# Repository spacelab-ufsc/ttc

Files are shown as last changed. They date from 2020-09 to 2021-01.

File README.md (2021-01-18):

<h1 align="center">
    TELEMETRY, TRACKING AND COMMAND
    <br>
</h1>

<h4 align="center">Telemetry, Tracking and Command module designed and developed by SpaceLab.</h4>

<p align="center">
	<a href="https://github.com/spacelab-ufsc/spacelab#versioning">
		
	</a>
	<a href="https://github.com/spacelab-ufsc/ttc/releases">
		
	</a>
	<a href="https://github.com/spacelab-ufsc/ttc/releases">
		
	</a>
	<a href="https://github.com/spacelab-ufsc/ttc/commits/master">
		
	</a>
	<a href="https://github.com/spacelab-ufsc/ttc/issues">
		
	</a>
	<a href="https://github.com/spacelab-ufsc/ttc/graphs/contributors">
		
	</a>
	<a href="#license">
		
	</a>
	<a href="https://github.com/floripasat/ttc">
		
	</a>
</p>

<p align="center">
    <a href="#overview">Overview</a> •
    <a href="#license">License</a> •
    <a href="#releases">Releases</a> •
</p>

<p align="center">
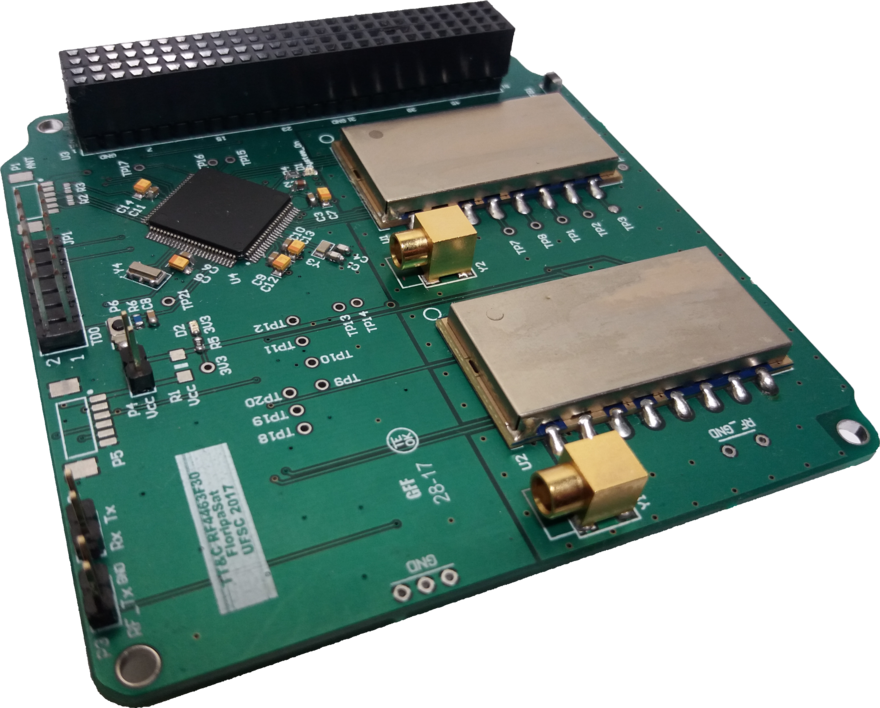
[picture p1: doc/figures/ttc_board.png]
    
</p>

## Overview

The TTC (or TT&C) is the communication module of the CubeSats from SpaceLab. It is responsible to make the communication between the earth (a ground station) and a satellite, and is divided in two sub-modules: Beacon and telemetry.

The beacon is a independent sub-module who transmits a periodic signal containing an identification data (ID) of the satellite and some basic telemetry data. The telemetry sub-module is the main communication device. It has a bidirectional data link to receive telecommands from the earth and transmit all the requested data. The telemetry sub-module is controlled by an external device (as example, an OBDH module).

## License

This project is open-source under three different licenses: GNU General Public License v3.0 for firmware sources, CERN Open Hardware License v2.0 for hardware files, and CC BY-SA 4.0 for the documentation. Some third-part files and libraries are subjected to their specific terms and licenses.

## Releases

The TTC software and hardware releases are synchronized in order to garantee compatibility. Then, using diferent versions might lead to unpredictable behavior. Refer to the [documentation](https://github.com/spacelab-ufsc/ttc/tree/master/doc) for compatibility notes.

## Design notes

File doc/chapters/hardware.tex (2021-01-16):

%
% hardware.tex
%
% Copyright (C) 2021 by SpaceLab.
%
% TTC Documentation
%
% This work is licensed under the Creative Commons Attribution-ShareAlike 4.0
% International License. To view a copy of this license,
% visit http://creativecommons.org/licenses/by-sa/4.0/.
%

%
% \brief Hardware description chapter.
%
% \author Gabriel Mariano Marcelino <gabriel.mm8@gmail.com>
%
% \institution Universidade Federal de Santa Catarina (UFSC)
%
% \version 1.2.0
%
% \date 2021/01/16
%

\chapter{Hardware} \label{ch:hardware}

The TTC board is composed by the following main components:

\begin{itemize}
	\item MSP430F6659, as the beacon microcontroller.
	\item RF4463F30, as the radio module for the beacon and the telemetry link.
\end{itemize}

In the figure \ref{fig:ttc-board}, ...

\begin{figure}[!h]
	\begin{center}
		
		\caption{TTC PCB.}
		\label{fig:ttc-board}
	\end{center}
\end{figure}

\section{General Diagram}

In the figure \ref{fig:hardware-diagram}, a general hardware diagram can be seen, with the connection and protocols between the components.

\begin{figure}[!h]
	\begin{center}
		
		\caption{Hardware diagram of the TTC module.}
		\label{fig:hardware-diagram}
	\end{center}
\end{figure}

\section{Main Components}

\subsection{Microcontroller}

The beacon microcontroller is the MSP430F6659IPZR \cite{msp430f6659}. Its main characteristics can be found in the table \ref{tab:msp430f6659-info}.

\nomenclature{\textbf{CPU}}{Central Processing Unit.}
\nomenclature{\textbf{RAM}}{Random Access Memory.}
\nomenclature{\textbf{GPIO}}{General Purpose Input/Output.}
\nomenclature{\textbf{I$^{2}$C}}{Inter-Integrated Circuit.}
\nomenclature{\textbf{SPI}}{Serial Peripheral Interface.}
\nomenclature{\textbf{UART}}{Universal Asynchronous Receiver/Transmitter.}
\nomenclature{\textbf{DMA}}{Direct Memory Access.}
\nomenclature{\textbf{ADC}}{Analog-To-Digital Converter.}
\nomenclature{\textbf{BSL}}{Bootstrap Loader.}

\begin{table}[!h]
	\begin{center}
		\begin{tabular}{lc}
			\toprule[1.5pt]
			\textit{Characteristic} & \textit{Value} \\
			\midrule
			CPU & MSP430 \\
			Frequency & Up to 20 MHz \\
			Non-volatile memory & 512 kB \\
			RAM & 66 kB \\
			GPIO pins & 74 \\
			I$^{2}$C & 3 \\
			SPI & 6 \\
			UART & 3 \\
			DMA & 6 \\
			ADC & ADC12-12ch \\
			Comparators & 12 inputs \\
			Timers - 16-bit & 4 \\
			Multiplier & $32 \times 32$ \\
			BSL & USB \\
			Min $V_{cc}$ & 1,8 V \\
			Max $V_{cc}$ & 3,6 V \\
			Active Power & $360\ \mu A/MHz$ \\
			Standby Power (LMP3) & $2,6\ \mu A$ \\
			Wakeup Time & $3\ \mu s$ \\
			Operating Temperature Range & -40 to 80 $^{\circ}C$ \\
			\bottomrule[1.5pt]
		\end{tabular}
		\caption{MSP430F6659 features.}
		\label{tab:msp430f6659-info}
	\end{center}
\end{table}

\subsection{Radio Modules}

The NiceRF RF4463F30 \cite{rf4463f30} is a transceiver module based on the Silicon Labs Si4463 \cite{si4463} radio. This module also contains a PA module to increase the output power up to 31 dBm.

In compliance with the \textit{TMR 3}, the RF4463F30 module operates with 5 V as input voltage in the TTC board, to achieve 30 dBm (1 W) in its output (The RF connector).

\subsubsection{Si4463}

The RF4463F30 module uses the Si4463 radio module. The main characteristics of this IC can be found in the table \ref{tab:si4463-info}.

\begin{table}[!h]
	\begin{center}
		\begin{tabular}{lcc}
			\toprule[1.5pt]
			\textit{Characteristic} & \textit{Value} & \textit{Unit} \\
			\midrule
			Frequency range & 119-1050 & MHz \\
			Receiver sensitivity & -126 & dBm \\
			Modulation & (G)FSK, 4(G)FSK, (G)MSK and OOK & - \\
			Max. output power & +20 & dBm \\
			PA support & +27 to 30 & dBm \\
			Ultra low current powerdown modes & 30 (shutdown), 50 (standby) & nA \\
			Data rate & 100 bps to 1 Mbps & - \\
			Power supply & 1,8 to 3,6 & V \\
			TX and RX FIFOs & 64 bytes for each or 129 bytes shared & - \\
			\bottomrule[1.5pt]
		\end{tabular}
		\caption{Si4463 features.}
		\label{tab:si4463-info}
	\end{center}
\end{table}

\section{External Connections}

This section describes the external available connections of the TTC module.

In the figure \ref{fig:connections-ref}, all the external connections are enumerated.

\begin{figure}[!h]
	\begin{center}
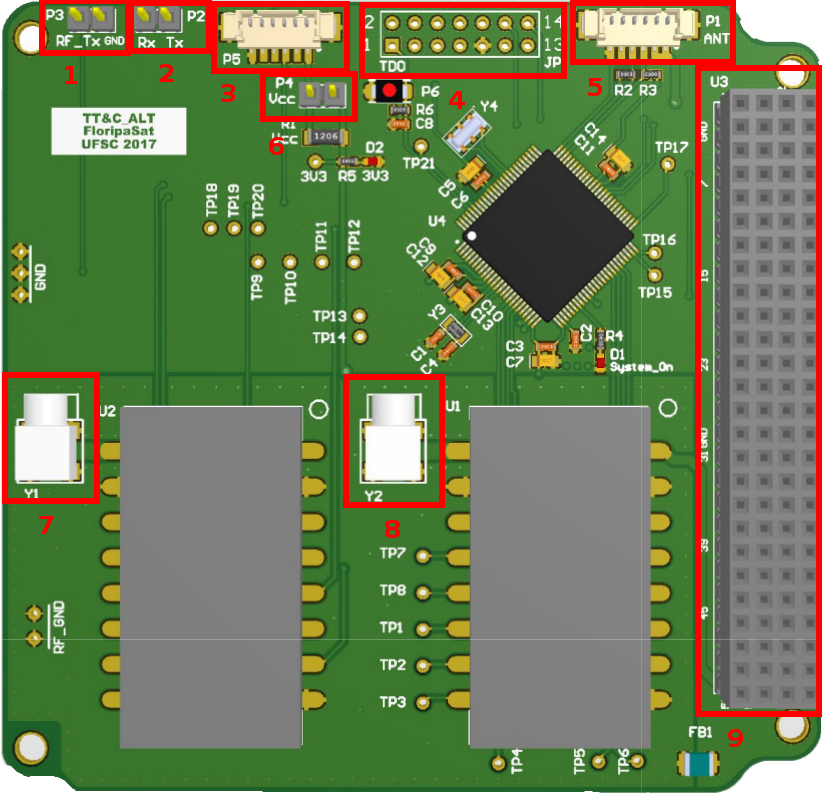
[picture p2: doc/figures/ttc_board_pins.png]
		
		\caption{External connections on the board.}
		\label{fig:connections-ref}
	\end{center}
\end{figure}

A brief description of each connection is presented in the table \ref{tab:connections-ref}.

\begin{table}[!h]
	\begin{center}
		\begin{tabular}{L{1.3cm} C{3cm} C{10cm}}
			\toprule[1.5pt]
			\textit{Number} & \textit{Connector} & \textit{Description} \\
			\midrule
			1 & Male pin header ($1 \times 2$) & UART TX $@$4800 bps. These pins transmit the beacon packets over a serial connection (It is enable in the configuration file, setting the BEACON\_RADIO variable as UART\_SIM). \\
			2 & Male pin header ($1 \times 2$) & Debug UART TX/RX $@$115200 bps. These pins transmit a description of the main events of the beacon software during it's execution. This feature is only available in DEBUG\_MODE. \\
			3 & Male PicoBlade$^{TM}$ ($\times 6$) & JTAG and Debug. This connection contains the relevant pins of the connectors 2 and 4. \\
			4 & Male pin header ($2 \times 2$) & MSP430 JTAG. This connection is for programming the uC code, using a MSP-FET debugger. \\
			5 & Male PicoBlade$^{TM}$ ($\times 6$) & Antenna I2C. I2C bus for a communication channel with the antenna module. \\
			6 & Male pin header ($1 \times 2$) & Power supply jumper. With a jumper, the beacon microcontroller power source comes from the JTAG connector. Without a jumper, the uC power supply comes from a pin of the PC104 connector. \\
			7 & Female Angled MCX & 437 MHz band RF signal (Goes to the antenna module). \\
			8 & Female Angled MCX & 145 MHz band RF signal (Goes to the antenna module). \\
			9 & Male/Female PCI-104 & PCI-104. Power supply and communication buses with others stacked up modules. \\
			\bottomrule[1.5pt]
		\end{tabular}
		\caption{External connections description.}
		\label{tab:connections-ref}
	\end{center}
\end{table}

The connections 1, 2, 4 and 6 were designed to be used during the software development stage, and not during the satellite operation.

\subsection{PCI-104 Pins}

The table \ref{tab:pci104-ref} describes the PCI-104 connector used pins. The first column is the row number of the connector, and the remaining columns are the respective columns (Named as H1A, H1B, H2A and H2B respectively). If the pin has no description, it is not connected to the TTC board.

\begin{table}[!h]
	\begin{center}
		\begin{tabular}{L{1cm} C{3cm} C{3cm} C{3cm} C{3cm}}
			\toprule[1.5pt]
			\textit{Row} & \textit{H1A} & \textit{H1B} & \textit{H2A} & \textit{H2B} \\
			\midrule
			1 & GND & GND & GND & GND \\
			2 & GND & GND & GND & GND \\
			3 & - & - & UART RX $@$4800 bps from the EPS module. & - \\
			4 & Telemetry radio GPIO0 & Telemetry radio GPIO1 & - & - \\
			5 & Telemetry radio GPIO2 & Enable beacon radio power supply & - & - \\
			6 & Telemetry radio SDN & - & OBDH communication (SPI MOSI) & OBDH communication (SPI clock) \\
			7 & - & - & OBDH communication (SPI chip select) & OBDH communication (SPI MISO) \\
			8 & - & - & - & - \\
			9 & - & - & - & - \\
			10 & - & - & - & - \\
			11 & - & - & - & - \\
			12 & - & - & - & - \\
			13 & - & - & - & - \\
			14 & - & - & Beacon uC power supply (3,3 V/50 mA) & 3,3 V beacon uC power supply (3,3 V/50 mA) \\
			15 & GND & GND & GND & GND \\
			16 & GND & GND & GND & GND \\
			17 & - & - & - & - \\
			18 & Telemetry radio SPI clock & - & - & - \\
			19 & Telemetry radio SPI MISO & - & - & - \\
			20 & Telemetry radio SPI MOSI & Telemetry radio SPI chip select & - & - \\
			21 & - & - & - & - \\
			22 & - & - & - & - \\
			23 & - & - & - & - \\
			24 & - & - & - & - \\
			25 & Telemetry radio power supply (5 V/500 mA) & - & - & - \\
			26 & Beacon radio power supply (5 V/500 mA) & - & - & - \\
			\bottomrule[1.5pt]
		\end{tabular}
		\caption{PCI-104 connector reference.}
		\label{tab:pci104-ref}
	\end{center}
\end{table}

\section{PCB}

The PCB (Printed Circuit Board) of the TTC module has basically the MSP430F6659 ic, the RF4463F30 module and all the external connectors.

Some characteristics of this PCB are described bellow:

\begin{itemize}
	\item The components and traces of the board are distributed over two layers (one in each side of the board).
	\item The RF modules are placed in a isolated ground plane (Connected to the main GND using a ferrite bead). This region can be seen in the figure \ref{fig:rf-ground-plane}.
	\item The antenna output of the RF4463F30 modules are connected to their respective connector over a 50 Ohm coupled trace.
\end{itemize}

\begin{figure}[!h]
	\begin{center}
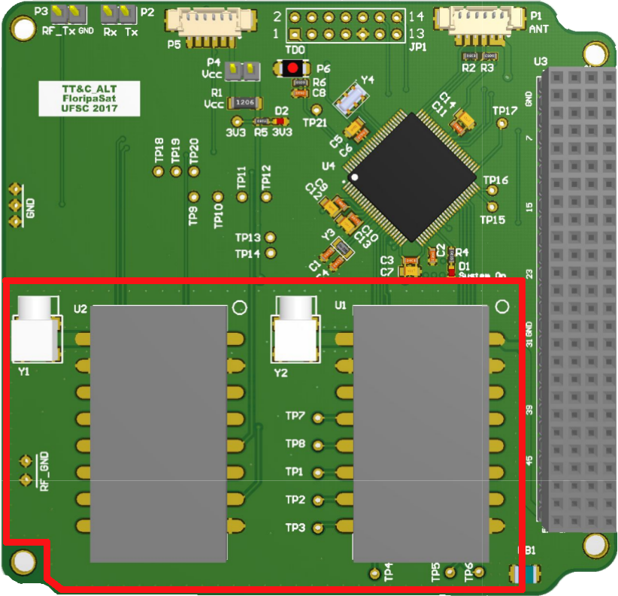
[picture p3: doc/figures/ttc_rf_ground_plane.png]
		
		\caption{RF ground plane region (red) of the TTC board.}
		\label{fig:rf-ground-plane}
	\end{center}
\end{figure}

\subsection{Types of assembly}

The TTC PCB has two types of assembly: Develop and flight.

The develop type has the purpose to be used during the development stage and tests. In this version, the connectors 3 and 5 are not soldered (Using the figure \ref{tab:connections-ref} as reference).

The flight version were designed to be used during the satellite operation. In this version, the connectors 1, 2, 4 and 6, and the reset button, are not soldered.

\section{Power Budget}

\begin{figure}[!h]
	\begin{center}
		
		\caption{Static power budget of the TTC module.}
		\label{fig:power-budget-static}
	\end{center}
\end{figure}

\begin{figure}[!h]
	\begin{center}
		
		\caption{Dynamic power budget of the TTC module.}
		\label{fig:power-budget-dynamic}
	\end{center}
\end{figure}

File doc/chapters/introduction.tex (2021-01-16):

%
% introduction.tex
%
% Copyright (C) 2021 by SpaceLab.
%
% TTC Documentation
%
% This work is licensed under the Creative Commons Attribution-ShareAlike 4.0
% International License. To view a copy of this license,
% visit http://creativecommons.org/licenses/by-sa/4.0/.
%

%
% \brief Introduction chapter.
%
% \author Gabriel Mariano Marcelino <gabriel.mm8@gmail.com>
%
% \institution Universidade Federal de Santa Catarina (UFSC)
%
% \version 1.2.0
%
% \date 2021/01/16
%

\chapter{Introduction} \label{ch:introduction}

This document is the general documentation of the Telemetry, Tracking and Command module of the FloripaSat project.

The TTC\nomenclature{\textbf{TTC}}{Telemetry, Tracking and Command.} (or TT\&C) is the communication module of the FloripaSat\cite{site} cubesat. It is responsible to make the communication between the earth (A ground station) and the satellite, and is divided in two sub-modules: Beacon and telemetry.

The beacon is a independent sub-module who transmits a periodic signal containing an identification data (ID) of the satellite and some basic telemetry data.

The telemetry sub-module is the main communication device. It has a bidirectional data link to receive telecommands from the earth and transmit all the requested data.

The telemetry sub-module is controlled by the OBDH\nomenclature{\textbf{OBDH}}{Onboard Data Handling.} module (The OBC\nomenclature{\textbf{OBC}}{Onboard Computer.} of the satellite), and the software for handling with this sub-module is under development in the OBDH module, and is not documented here.

\nomenclature{\textbf{PCB}}{Printed Circuit Board.}
\nomenclature{\textbf{USB}}{Universal Serial Bus.}

\cite{github}

The beacon executes the following tasks during its execution:

\begin{itemize}
	\item 145 MHz band antenna deployment.
	\item One-way communication (RX) with the EPS module, using the FSP protocol.
	\item Two-way communication (TX and RX) with the OBDH module, using the FSP protocol.
	\item Transmission of the beacon packets (In two protocols: NGHam and AX.25), containing the data from the EPS or the OBDH module and the satellite ID (``FLORIPASAT").
	\item When required by the OBDH module, the transmissions are stopped for an hibernation period (shutdown).
	\item In case of an critical failure of the OBDH module, or the uplink channel, the beacon activates its reception and is capable of make its own hibernation (shutdown).
\end{itemize}

\section{Module Requirements}

In the list below, the TTC module requirements for the mission are described. These requirements are nominated as TMR\nomenclature{\textbf{TMR}}{Telemetry, Tracking and Command Module Requirements.}, or Telemetry, Tracking and Command Module Requirements.

\begin{enumerate}[label=\textit{TMR \arabic*}, leftmargin=*, align=left]
	\item The FloripaSat shall have a physical device to inhibit radio frequency (RF\nomenclature{\textbf{RF}}{Radio Frequency.}) transmission.
	
	\begin{footnotesize}
		Compliance with CDS\nomenclature{\textbf{CDS}}{CubeSat Design Specification.} 3.3.9: The use of three independent inhibits is highly recommended and can reduce required documentation and analysis.	
	\end{footnotesize}
	
	\item The CubeSat will have the RF power output to the transmitting antenna input no greater than 1,5 W.
	
	\begin{footnotesize}
		Compliance with CDS 3.3.9.1.
	\end{footnotesize}
	
	\item The CubeSat will have the RF power output to the transmitting antenna input no less than 1,0 W (or 30 dBm).
	
	\begin{footnotesize}
		Defined by team analysis.
	\end{footnotesize}
	\item No CubeSats shall generate or transmit any RF signal from the time of integration into the P-POD\nomenclature{\textbf{P-POD}}{Poly-Picosatellite Orbital Deployer.} through 45 minutes after on-orbit deployment from the P-POD.
	
	\begin{footnotesize}
		Compliance with CDS.
	\end{footnotesize}
	
	\item TTC transceiver shall transmit and receive on the frequency of 437,9 Mhz.
	
	\begin{footnotesize}
		Defined by the team, based on available spectrum allocation to Amateur communication.
	\end{footnotesize}
	
	\item TTC beacon shall transmit on the frequency of 145,9 Mhz.
	
	\begin{footnotesize}
		Defined by the team, based on available spectrum allocation to Amateur communication.
	\end{footnotesize}
	
	\item TTC shall modulate and demodulate information using GFSK\nomenclature{\textbf{GFSK}}{Gaussian Frequency-Shift Keyring.}.
	
	\begin{footnotesize}
		Defined by the team.
	\end{footnotesize}
	
	\item TTC Beacon must transmit periodic beacon messages at an interval of 10
seconds, except when in hibernation or shutdown mode. Allows ground stations to track and receive satellite data even if telecommand was not sent to the satellite.
	\item TTC transceiver must receive signals from ground stations and demodulate them.
	\item TTC must interface with OBDH, exchanging encoded raw data received or to be transmitted.
	\item TTC must interface with OBDH using the SPI protocol ($@$2 KHz).
	
	\begin{footnotesize}
		Defined by the team.
	\end{footnotesize}
	
	\item TTC radio must modulate raw data received from OBDH using GFSK, prior to transmission, and demodulate received data and forward raw data to OBDH.
	\item TTC transceiver shall transmit and receive data at a baud rate of 2400 bps. Defined by the team, based on link budget analysis.
	\item TTC beacon shall transmit data at a baud rate of 1200 bps.
	
	\begin{footnotesize}
		Defined by the team, based on link budget analysis.
	\end{footnotesize}
	
	\item TTC beacon shall transmit packets using the NGHam and AX.25 protocols.
	
	\begin{footnotesize}
		Defined by the team.
	\end{footnotesize}
	
	\item A same beacon packet must be transmitted in both NGHam and AX.25 protocols.
	
	\begin{footnotesize}
		Defined by the team.
	\end{footnotesize}
	
	\item TTC must receive the batteries voltages from the EPS module at every 10 seconds.
	
	\begin{footnotesize}
		Defined by the team.
	\end{footnotesize}
	
	\item The payload from the packets transmitted by the beacon must contain at least the satellite ID ("FLORIPASAT") and batteries voltages (received from the EPS module at every 10 seconds).
	\item TTC uC must perform the antenna deployment of the VHF band antenna.
	
	\begin{footnotesize}
		Defined by the team.
	\end{footnotesize}
	
	\item Between the beacon packets transmissions, the beacon MCU and radio must operate in low power mode, to save energy.
	
	\begin{footnotesize}
		Defined by the team.
	\end{footnotesize}
	
	\item TTC PAs (Power amplifiers) must just only be activated during transmissions. When they are not in operation, they must be turned off.
	
	\begin{footnotesize}
		Defined by the team.
	\end{footnotesize}
	
	\item All the beacon critical data, like time control and antenna deployment status, must be stored in a non-volatile memory.
	
	\begin{footnotesize}
		Defined by the team.
	\end{footnotesize}
	
	\item TTC beacon must be able to receive a 24 hour shutdown command from the OBDH module.
	
	\begin{footnotesize}
		Compliance with AMSAT/IARU regulations.
	\end{footnotesize}
	
\end{enumerate}

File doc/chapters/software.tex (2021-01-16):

%
% software.tex
%
% Copyright (C) 2021 by SpaceLab.
%
% TTC Documentation
%
% This work is licensed under the Creative Commons Attribution-ShareAlike 4.0
% International License. To view a copy of this license,
% visit http://creativecommons.org/licenses/by-sa/4.0/.
%

%
% \brief Software description chapter.
%
% \author Gabriel Mariano Marcelino <gabriel.mm8@gmail.com>
%
% \institution Universidade Federal de Santa Catarina (UFSC)
%
% \version 1.2.0
%
% \date 2021/01/16
%

\chapter{Software} \label{ch:software}

The beacon software is responsible to transmit periodic beacon signals, containing the satellite identification and a basic telemetry data.

To achieve it, this software communicates with other modules of the satellite (to acquire data to transmit in the beacon packets), controls the beacon's radio module and its antenna module.

It's written in C, using the Code Composer Studio IDE (Version 7.4.0). The radio module (Si4463 IC) is configured using the WDS (Version 3.2.11), a step-by-step tutorial is available as an apendix.

\section{Dependencies}

The beacon software is dependent of the following libraries:

\begin{itemize}
    \item NGHam: Used to generate and interpret the NGHam protocol packets (This library was modified for this firmware).
    \item DriverLib: Used to handle the internal peripherals of the MSP430F6659 uC.
\end{itemize}

\nomenclature{\textbf{HAL}}{Hardware Abstraction Layer.}

\section{Software Layers}

The figure \ref{fig:beacon-software-layers} describes the software layers of the beacon system.

\begin{figure}[!h]
	\begin{center}
		
		\caption{Beacon software stack-up.}
		\label{fig:beacon-software-layers}
	\end{center}
\end{figure}

It is composed by five layers:

\begin{itemize}
    \item Hardware layer: All the TTC hardware (MSP430F6659 and the RF4463F30).
    \item Drivers layer: The software to make the interface with the hardware (Internal peripherals of the uC, the radio module and the antenna module).
    \item System layer: General usage functions and resources of the beacon system (like data structures, power management, etc.).
    \item Application layer: The main beacon software, where all the tasks were implemented.
\end{itemize}

\section{Flowcharts}

\subsection{Main}

\begin{figure}[!h]
	\begin{center}
		
		\caption{Main flowchart of the beacon software.}
		\label{fig:beacon-main-flowchart}
	\end{center}
\end{figure}

\subsection{Initialization}

\begin{figure}[!h]
	\begin{center}
		
		\caption{Flowchart of the beacon initialization.}
		\label{fig:beacon-init-flowchart}
	\end{center}
\end{figure}

\subsubsection{Watchdog}

The watchdog is initialized using the ACLK as clock source and a 512k clock divider (generating a 16 second watchdog). The counter starts right after the initialization.

\subsubsection{CPU}

For the CPU configuration, the core voltage is setted to level 2 (required for a clock between 12 and 20 MHz). The DCO FLL reference is setted to REF0 (with the clock divider equal to 1). The ACLK clock is setted to be equal to REF0 (same as DCO, clock divider equal to 1). The SMCLK reference is setted to be the DCO, but with a divider factor equal to 4.

So, the final configuration is: MCLK = 16 MHz, SMCLK = 4 MHz and ACLK = 32,768 kHz.

\subsubsection{Memory}

UNDER DEVELOPMENT.

\subsubsection{Time}

During the time initialization, the last value stored in the memory is loaded and the counter continues from it value, preventing the lost of time reference after a system reboot or fault.

\subsubsection{Timer}

For the system time, a 1 second timer is used (using the timer interruption to increment a second counter variable, 32-bit unsigned integer). This counting starts from the last value stored into the memory.

\subsubsection{Antenna}

UNDER DEVELOPMENT.

\subsubsection{EPS Communication Bus}

The EPS communication bus (UART) is configured at a transfer rate of 4800 bps, no parity bit, LSB first and one stop bit. The clock source of this UART bus is the SMCLK. The EPS queue is also initialized.

\subsubsection{OBDH Communication Bus}

The same occurs for the OBDH communication bus (SPI): the transfer rate is 2400 bps and the endianness is MSB first. The OBDH queue is also initialized.

\subsubsection{Radio}

During the initialization of the radio, it is reseted and all the configuration parameters are transfered to the radio module. More informations about this process can be found in the radio IC documentation.

\subsubsection{RF Protocols}

The NGHam, AX.25 and the FSP protocols also need an initialization, to set internal variables and counters.

\subsection{ISRs}

\nomenclature{\textbf{ISR}}{Interruption Service Routine.}

\subsubsection{OBDH and EPS Communication}

The flowchart of the interruption service routine (ISR) of the OBDH communication can be seen in the figure \ref{fig:beacon-obdh-isr-flowchart}. Basically, when a new byte arrives, it is pushed to a queue (if it isn't full), and periodically, the OBDH communication task process these new bytes (taking out the bytes from the queue).

The flowchart of the interruption service routine (ISR) of the EPS communication can be seen in the figure \ref{fig:beacon-eps-isr-flowchart}. It's operation is equal to the OBDH communication ISR.

\begin{figure}[!h]
	\begin{center}
		\subfigure[OBDH communication ISR flowchart.\label{fig:beacon-obdh-isr-flowchart}]{}
		\qquad
		\subfigure[EPS communication ISR flowchart.\label{fig:beacon-eps-isr-flowchart}]{}
		\caption{OBDH and EPS modules comunication ISRs routines.}
		\label{fig:obdh-eps-isr-flowchart}
	\end{center}
\end{figure}

\section{Operation Modes}

There are three operation modes in the beacon software:

\begin{itemize}
    \item DEBUG MODE: In this mode, the operation of the beacon is described through an UART port. At every operation, a message describing what is happening is transmitted to the debug UART port.
    \item TEST MODE: In this mode, the antenna deployment routines are not executed. This is the main mode to use during the satellite integration tests.
    \item FLIGHT MODE: This is the mode to use in flight, with all the available resources enabled.
\end{itemize}

The selection of the operation mode can be done using the ``BEACON\_MODE" variable in the ``config.h" file.

\section{Tasks}

In the table \ref{tab:sw_tasks}, the beacon tasks are listed with a brief description and its period of execution.

\begin{table}[!h]
	\begin{center}
		\begin{tabular}{L{0.2\textwidth} C{0.4\textwidth} C{0.3\textwidth}}
			\toprule[1.5pt]
			\textit{Task} & \textit{Description} & \textit{Period} \\
			\midrule
			System initialization & Submodules initialization (CPU, memory, radio, etc.) & Aperiodic (Executed only at initializations) \\
			Antenna deployment & 145 MHz band antenna deployment after the satellite launch & Aperiodic (Executed once) \\
			NGHam packet transmission & Transmission of the beacon packets with a basic telemetry data using the NGHam protocol & 10, 20 or 30 seconds (EPS energy level dependent) \\
			AX.25 packet transmission & Transmission of the beacon packets with a basic telemetry data using the AX.25 protocol & 10, 20 or 30 seconds (EPS energy level dependent) \\
			OBDH data processing & The OBDH module can send telemetry data or commands & Aperiodic (OBDH module dependent) \\
			EPS data processing & The EPS modules sends telemetry data & Aperiodic (EPS module dependent) \\
			Radio data processing & Processing of an incoming packet from the beacon radio & Aperiodic (Only when the OBDH fails and an hibernation is required) \\
			Beacon radio reception activation & When a critical failure occur in the OBDH module, the beacon activates its reception between the beacon transmissions & Aperiodic (Only when the OBDH module fails) \\
			Radio reset & Beacon radio reset & 10 minutes \\
			Beacon reset & Beacon system reset & 12 hours \\
			\bottomrule[1.5pt]
		\end{tabular}
		\caption{Beacon software tasks.}
		\label{tab:sw_tasks}
	\end{center}
\end{table}

\section{Packets Payload}

In the normal satellite operation, the beacon packets contains the data from the table \ref{tab:beacon-normal-payload}.

\begin{table}[!h]
	\begin{center}
		\begin{tabular}{lc}
			\toprule[1.5pt]
			\textit{Information} & \textit{Length (Bytes)} \\
			\midrule
			Satellite ID: ``FLORIPASAT" & 10 \\
			Batteries voltages & 4 \\
			Batteries temperatures & 6 \\
			Total charge of batteries & 2 \\
			Solar panels currents & 12 \\
			Solar panels voltages & 6 \\
			Overall status of the satellite & 2 \\
			Accelerometer and gyroscope & 12 \\
			Time since boot & 4 \\
			Number of OBDH module resets since launch & 2 \\
			\bottomrule[1.5pt]
		\end{tabular}
		\caption{Normal content of the beacon packets.}
		\label{tab:beacon-normal-payload}
	\end{center}
\end{table}

If a fault on the OBDH module occurs, only the EPS data are transmitted, the contents of this kind of packet can be seen in the table \ref{tab:beacon-without-obdh-payload}.

\begin{table}[!h]
	\begin{center}
		\begin{tabular}{lc}
			\toprule[1.5pt]
			\textit{Information} & \textit{Length (Bytes)} \\
			\midrule
			Satellite ID: ``FLORIPASAT" & 10 \\
			Batteries voltages & 4 \\
			Batteries temperatures & 6 \\
			Total charge of batteries & 2 \\
			Solar panels currents & 12 \\
			Solar panels voltages & 6 \\
			Energy level & 1 \\
			\bottomrule[1.5pt]
		\end{tabular}
		\caption{Content of the beacon packets with a fault in the OBDH module.}
		\label{tab:beacon-without-obdh-payload}
	\end{center}
\end{table}

If a fault occurs in the OBDH and the EPS modules, only the satellite ID is transmitted. It can be seen in the table \ref{tab:beacon-without-eps-payload}.

\begin{table}[!h]
	\begin{center}
		\begin{tabular}{lc}
			\toprule[1.5pt]
			\textit{Information} & \textit{Length (Bytes)} \\
			\midrule
			Satellite ID: ``FLORIPASAT" & 10 \\
			\bottomrule[1.5pt]
		\end{tabular}
		\caption{Content of the beacon packets with a fault in the OBDH and EPS modules.}
		\label{tab:beacon-without-eps-payload}
	\end{center}
\end{table}

The decodification of the packets data are done automatically by the GRS software.

\section{USCIs Configuration}

\begin{table}[!h]
	\begin{center}
		\begin{tabular}{lcc}
			\toprule[1.5pt]
			\textit{MSP Interface} & \textit{Mode} & \textit{Connected Components} \\
			\midrule
			USCI\_A0 & UART RX & EPS Bus \\
			USCI\_A0 & UART TX & Packets transmission (Only for tests) \\
			USCI\_A1 & UART TX/RX & Debug \\
			USCI\_A2 & SPI Slave & OBDH Bus \\
			USCI\_B0 & SPI Master & Beacon transceiver \\
			USCI\_B2 & $I^{2}C$ Master & Antenna bus  \\
			\bottomrule[1.5pt]
		\end{tabular}
		\caption{USCIs configuration of the beacon microcontroller.}
		\label{tab:beacon-uc-usci-config}
	\end{center}
\end{table}

\section{Timers}

\begin{table}[!h]
	\begin{center}
		\begin{tabular}{lccc}
			\toprule[1.5pt]
			\textit{Timer Interface} & \textit{Mode} & \textit{Period} & \textit{Function} \\
			\midrule
			TIMER\_A1 & Continuous-Compare & 1 s & Time Control \\
			\bottomrule[1.5pt]
		\end{tabular}
		\caption{Timers configuration of the beacon microcontroller.}
		\label{tab:beacon-uc-timers-config}
	\end{center}
\end{table}

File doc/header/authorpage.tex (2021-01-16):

%
% authorpage.tex
%
% Copyright (C) 2021 SpaceLab.
%
% TTC Documentation
%
% This work is licensed under the Creative Commons Attribution-ShareAlike 4.0
% International License. To view a copy of this license,
% visit http://creativecommons.org/licenses/by-sa/4.0/.
%

%
% \brief Author page.
%
% \author Gabriel Mariano Marcelino <gabriel.mm8@gmail.com>
%
% \institution Universidade Federal de Santa Catarina (UFSC)
%
% \version 1.2.0
%
% \date 2021/01/16
%

\thispagestyle{empty}

\begin{center}

\textbf{\thetitle}

\textit{January, 2021}

\vspace{1cm}

\textbf{Project Chief:}

Eduardo Augusto Bezerra

\vspace{1cm}

\textbf{Authors:}

Gabriel Mariano Marcelino \\

\vspace{1cm}

\textbf{Contributing Authors:}

Sara Vega Martinez \\

\vspace{1cm}

\textbf{Revision Control:}

\end{center}

\begin{table}[!ht]
    \begin{center}
        \begin{tabular}{cL{5cm}L{5.5cm}C{2cm}}
            \toprule[1.5pt]
            \textbf{Version} & \textbf{Author}  & \textbf{Changes}    & \textbf{Date} \\
            \midrule
            1.2     & G. M. Marcelino           & Template update     & 2021/01/16 \\
                    &                           &                     &            \\
                    &                           &                     &            \\
                    &                           &                     &            \\
            \bottomrule[1.5pt]
        \end{tabular}
    \end{center}
\end{table}

\vfill

\begin{figure}[!h]
	\begin{center}
		
	\end{center}
\end{figure}

\textcopyright\  2021 by SpaceLab. \thetitle. This work is licensed under the Creative Commons Attribution-ShareAlike 4.0 International License. To view a copy of this license, visit \href{http://creativecommons.org/licenses/by-sa/4.0/}{http://creativecommons.org/licenses/by-sa/4.0/}.

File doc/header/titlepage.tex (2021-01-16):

%
% titlepage.tex
%
% Copyright (C) 2021 by SpaceLab.
%
% TTC Documentation
%
% This work is licensed under the Creative Commons Attribution-ShareAlike 4.0
% International License. To view a copy of this license,
% visit http://creativecommons.org/licenses/by-sa/4.0/.
%

%
% \brief Title page.
%
% \author Gabriel Mariano Marcelino <gabriel.mm8@gmail.com>
%
% \institution Universidade Federal de Santa Catarina (UFSC)
%
% \version 1.2.0
%
% \date 2021/01/16
%

\begin{titlepage}

\thispagestyle{empty}

\begin{flushleft}
SLB-TTC-DOC-v1.2
\end{flushleft}

\vspace{1cm}

\begin{figure}[!ht]
    \begin{flushleft}
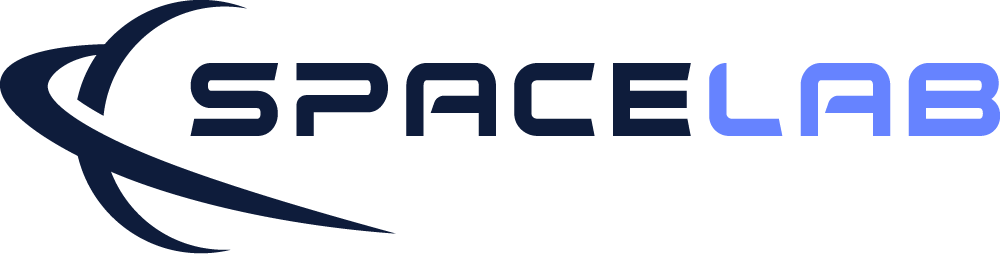
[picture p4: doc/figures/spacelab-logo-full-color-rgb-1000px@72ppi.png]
        
    \end{flushleft}
\end{figure}

\begin{flushleft}
\Huge{\textbf{\thetitle}}
\rule[0pt]{\textwidth}{5pt}
\end{flushleft}

\vspace{0.2cm}

\begin{flushleft}
\textit{\thetitle} \\
\textit{SpaceLab, Universidade Federal de Santa Catarina, Florianópolis - Brazil}
\end{flushleft}

\vfill
\vfill

\begin{flushright}
January 2021
\end{flushright}

\end{titlepage}

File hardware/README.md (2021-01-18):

<h1 align="center">
    TTC HARDWARE
    <br>
</h1>

<h4 align="center">Telemetry, Tracking and Command module hardware project (sources, outputs, and documentation).</h4>

<p align="center">
    <a href="https://github.com/spacelab-ufsc/spacelab#versioning">
        
    </a>
    <a href="https://github.com/spacelab-ufsc/ttc/releases">
        
    </a>
    <a href="https://github.com/spacelab-ufsc/ttc/releases">
        
    </a>
    <a href="https://github.com/spacelab-ufsc/ttc/commits/master">
        
    </a>
    <a href="https://github.com/spacelab-ufsc/ttc/issues">
        
    </a>
    <a href="">
        
    </a>    
    <a href="#license">
        
    </a>
    <a href="https://github.com/floripasat/ttc">
        
    </a>
</p>

<p align="center">
    <a href="#overview">Overview</a> •
    <a href="#version">Version</a> •
    <a href="#license">License</a>
</p>

## Overview

The TTC (or TT&C) is the communication module of the CubeSats from SpaceLab. It is responsible to make the communication between the earth (a ground station) and a satellite, and is divided in two sub-modules: Beacon and telemetry.

This folder contains the hardware project of the TTC board.

## Version

Refer to the [releases](https://github.com/spacelab-ufsc/ttc/releases) page.

## License

This repository containing hardware files is licensed under CERN Open Hardware License, version 2.

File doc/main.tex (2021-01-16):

%
% main.tex
%
% Copyright (C) 2021 by SpaceLab.
%
% TTC Documentation
%
% This work is licensed under the Creative Commons Attribution-ShareAlike 4.0
% International License. To view a copy of this license,
% visit http://creativecommons.org/licenses/by-sa/4.0/.
%

%
% \brief Main file.
%
% \author Gabriel Mariano Marcelino <gabriel.mm8@gmail.com>
%
% \institution Universidade Federal de Santa Catarina (UFSC)
%
% \version 1.2.0
%
% \date 2021/01/16
%

\documentclass[a4paper,12pt]{book}

\usepackage{spacelab_book}

\title{TTC Documentation}
\author{SpaceLab}
\date{\today}

% File metadata
\hypersetup
{
    pdfauthor   = {SpaceLab},
    pdfsubject  = {\thetitle},
    pdftitle    = {\thetitle},
    pdfkeywords = {Nanosatellites, CubeSats, Telecommunications, TTC}
}

\begin{document}

    \pagenumbering{roman}
    \setcounter{page}{1}

    \input{header/titlepage}
    \cleardoublepage
    \input{header/authorpage}
    \cleardoublepage

    \listoffigures
    \addcontentsline{toc}{chapter}{List of Figures}

    \listoftables
    \addcontentsline{toc}{chapter}{Lista of Tables}

    \printnomenclature
    \addcontentsline{toc}{chapter}{Nomenclature}

    \tableofcontents
    \cleardoublepage
    
    \pagenumbering{arabic}
    \setcounter{page}{1}

    \input{chapters/introduction}
    \input{chapters/hardware}
    \input{chapters/software}
    \input{chapters/tests}
    \input{chapters/assembly}
    \input{chapters/references}

\end{document}

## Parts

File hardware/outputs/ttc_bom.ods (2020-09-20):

Item | Designator | Quantity | Manufacturer | Partnumber | Decription | Package/footprint | Type
1 | C1, C4 | 2 | Murata | GQM1875C2E120GB12D | Multilayer Ceramic Capacitors MLCC - SMD/SMT 0603 12pF 250volts C0G 2% | 0603 | SMD/SMT
2 | C2 | 1 | TDK | C1608X7R1H474K080AE | Multilayer Ceramic Capacitors MLCC - SMD/SMT SOFT 0603 50V 0.47uF X7R 10% T: 0.85mm | 0603 | SMD/SMT
3 | C3, C6, C9, C10, C11 | 5 | Kemet | C0603C104K5RAL | Multilayer Ceramic Capacitors MLCC - SMD/SMT 50V 0.1uF 0603 X7R 10% | 0603 | SMD/SMT
4 | C5, C7, C12, C13, C14 | 5 | AVX | TPSR106K006R1000 | Tantalum Capacitors - Solid SMD 6.3V 10uF 10% 0805 ESR= 1 Ohm | 0805 | SMD/SMT
5 | C8 | 1 | AVX | 02013D222KAT2A | Multilayer Ceramic Capacitors MLCC - SMD/SMT 25V 2200pF X5R 0201 10% | 0603 | SMD/SMT
6 | FB1 | 1 | Murata | BLE32PN300SN1L | Ferrite Beads 1210 30ohms10A +/-10ohms | 1210 | SMD/SMT
7 | P1, P5 | 2 | Molex | 53398-0671 | Headers & Wire Housings VERTICAL HDR SMT 6P | Connector | SMD/SMT
8 | R1 | 1 | Vishay | CRCW12060000Z0EAHP | Thick Film Resistors - SMD 3/4W Zeroohm Jumper High Power AEC-Q200 | 1206 | SMD/SMT
9 | R2, R3 | 2 | Vishay | MCT0603MC1002FP500 | Thin Film Resistors - SMD .15W 10Kohms 1% 0603 50ppm Auto | 0603 | SMD/SMT
10 | R4 | 1 | Vishay | CRCW0603330RFKEAHP | Thick Film Resistors - SMD 0.33W 330ohms 1% High Power AEC-Q200 | 0603 | SMD/SMT
11 | R6 | 1 | Rohm | SFR03EZPF4702 | Thick Film Resistors - SMD 0603 47Kohm 1% Anti-Sulfur AEC-Q200 | 0603 | SMD/SMT
12 | U3 | 2 | Samtec | TSW-126-07-G-D | Headers & Wire Housings .100" Terminal Strip | Connector | Through hole
13 | U4 | 1 | Texas Instruments | MSP430F6659IPZR | 16-bit Microcontrollers - MCU Mixed Signal MCU | LQFP-100 | SMD/SMT
14 | Y1, Y2 | 2 | TE Connectivity | 1-1337583-0 | RF Connectors / Coaxial Connectors R/A SMT Skt 50Ohm Gold Pltd | Connector | SMD/SMT
15 | Y3 | 1 | Abracon | ABS06-32.768KHZ-T | Crystals 32.768KHz 20ppm 12.5pF -40C +85C | 2 mm x 1.2 mm | SMD/SMT
16 | Y4 | 1 | Murata | CSTNR4M00GH5L000R0 | Resonators 4.0000MHz 39pF SMD CHP Resntr Tol 0.07% | - | SMD/SMT
17 | U1 | 1 | NiceRF | RF4463F30-433 | RF4463F30 High Power Wireless Transceiver Module | - | SMD/SMT
18 | U2 | 1 | NiceRF | RF4463F30-170 | RF4463F30 High Power Wireless Transceiver Module | - | SMD/SMT

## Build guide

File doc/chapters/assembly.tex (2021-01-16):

%
% assembly.tex
%
% Copyright (C) 2021 by SpaceLab.
%
% TTC Documentation
%
% This work is licensed under the Creative Commons Attribution-ShareAlike 4.0
% International License. To view a copy of this license,
% visit http://creativecommons.org/licenses/by-sa/4.0/.
%

%
% \brief Assembly instructions chapter.
%
% \author Gabriel Mariano Marcelino <gabriel.mm8@gmail.com>
%
% \institution Universidade Federal de Santa Catarina (UFSC)
%
% \version 1.2.0
%
% \date 2021/01/16
%

\chapter{Assembly Instructions} \label{ch:assembly}

\section{Radio Configuration}

This appendix is a tutorial with the purpose of generate a source code file with basic configuration parameters of the radio module. For it, the WDS software from Silicon Labs will be used (version 3.2.11.0).

Unfortunately, the software in only available for Windows platforms.

\subsection{Steps}

After the installation of the software, the procedures to configure the beacon radio are described bellow (When a parameter to configure the telemetry link radio differs from the beacon radio, a note describes the difference).

\subsubsection{Step 1}

\begin{enumerate}
    \item Open the WDS software.
    \item The following box will appear in the center of the window.
    \item Click in "Simulate radio" and go to the next step.
\end{enumerate}

\begin{figure}[!h]
	\begin{center}
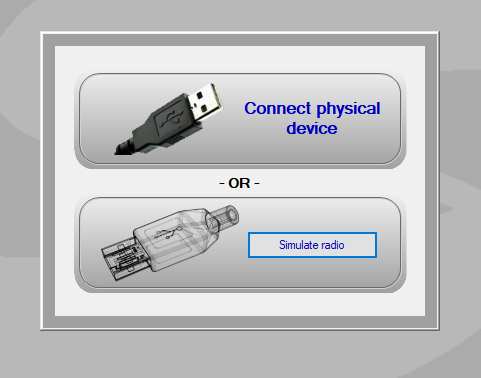
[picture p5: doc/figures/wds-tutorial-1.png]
		
		\caption{Step 1 of the radio configuration.}
		\label{fig:wds-tutorial-step-1}
	\end{center}
\end{figure}

\subsubsection{Step 2}

\begin{enumerate}
    \item In the list of radios that appeared on the new window, select the chip type ``Si4463".
    \item In the revision column, select ``B1".
    \item Click on ``Select Radio" to go to the next step.
\end{enumerate}

\begin{figure}[!h]
	\begin{center}
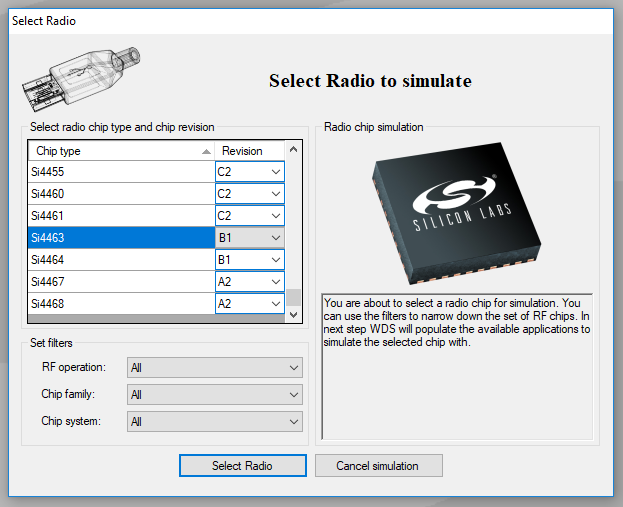
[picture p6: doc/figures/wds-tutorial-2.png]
		
		\caption{Step 2 of the radio configuration.}
		\label{fig:wds-tutorial-step-2}
	\end{center}
\end{figure}

\subsubsection{Step 3}

\begin{enumerate}
    \item Select ``Radio Configuration Application".
    \item Click on ``Select Application" to go to the next step.
\end{enumerate}

\begin{figure}[!h]
	\begin{center}
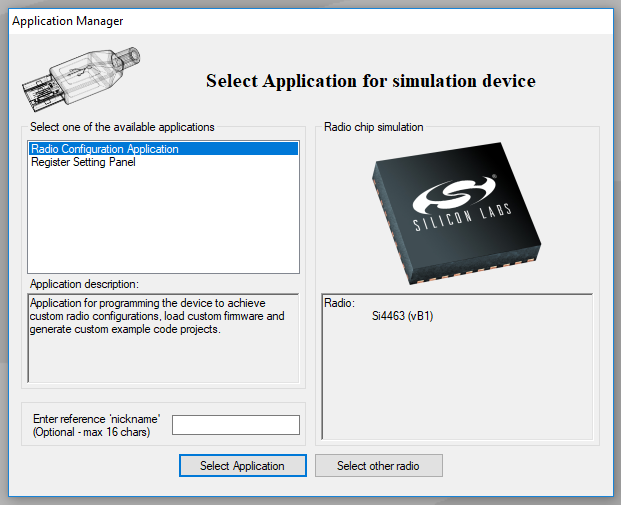
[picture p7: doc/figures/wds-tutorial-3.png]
		
		\caption{Step 3 of the radio configuration.}
		\label{fig:wds-tutorial-step-3}
	\end{center}
\end{figure}

\subsubsection{Step 4}

\begin{enumerate}
    \item In the ``Frequency and power" tab, change the base frequency to 145,9 MHz.
    \item Change the channel spacing to 0 kHz.
    \item Change the crystal tolerance to 10,0 ppm (Both RX and TX).
    \item Go to the next step.
\end{enumerate}

\begin{figure}[!h]
	\begin{center}
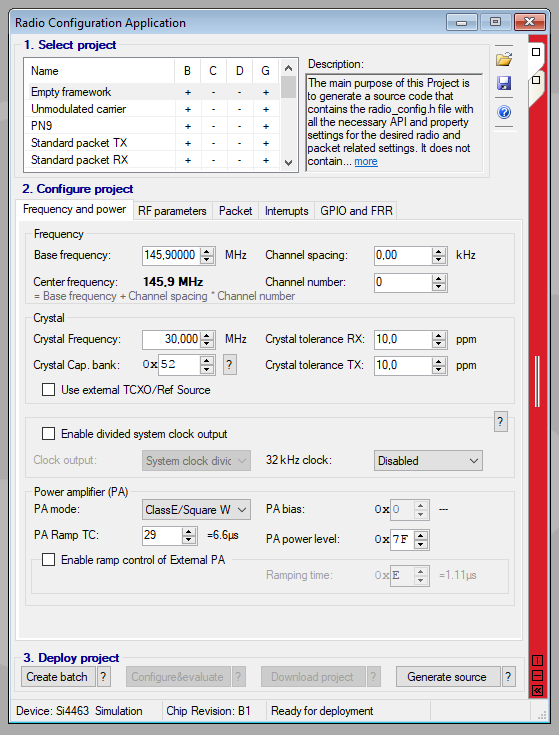
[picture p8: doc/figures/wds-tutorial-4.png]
		
		\caption{Step 4 of the radio configuration.}
		\label{fig:wds-tutorial-step-4}
	\end{center}
\end{figure}

\subsubsection{Step 5}

\begin{enumerate}
    \item In the ``RF parameters" tab, change the modulation type to ``2GFSK".
    \item Change the the data rate to 1,2 kbps.
    \item Change the deviation to $2,5\ kHz$.
    \item Go to the next step.
\end{enumerate}

\begin{figure}[!h]
	\begin{center}
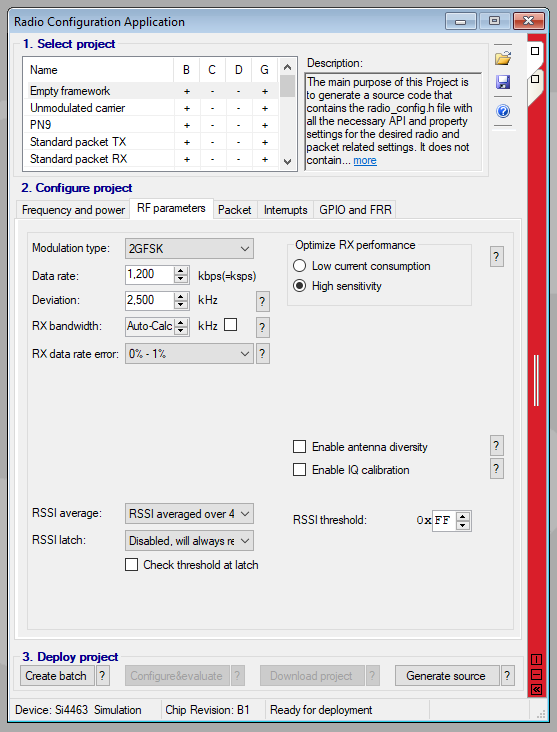
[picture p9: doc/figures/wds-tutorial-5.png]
		
		\caption{Step 5 of the radio configuration.}
		\label{fig:wds-tutorial-step-5}
	\end{center}
\end{figure}

\subsubsection{Step 6}

\begin{enumerate}
    \item In the ``Packet" tab, many subtabs will appear. In ``Preamble" change the ``Preamble TX length" to 4 bytes.
    \item Again, in ``Preamble", change the ``Preamble pattern" to ``Std. 1010 pattern (>= 32 and < 40 bits)".
    \item Go to the next step.
\end{enumerate}

\begin{figure}[!h]
	\begin{center}
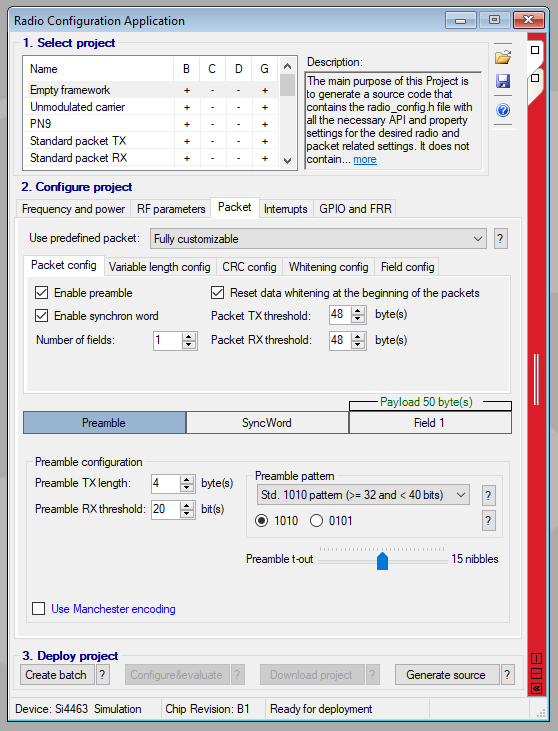
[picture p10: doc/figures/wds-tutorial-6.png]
		
		\caption{Step 6 of the radio configuration.}
		\label{fig:wds-tutorial-step-6}
	\end{center}
\end{figure}

\subsubsection{Step 7}

\begin{enumerate}
    \item In the ``Sync Word" tab, change the sync word length field to ``4 bytes".
    \item In the ``Sync Word (on air int.)", enter the following sequence: 5D E6 2A 7E. This sequence is the sync word used by the NGHam protocol.
    \item Go to the next step.
\end{enumerate}

\begin{figure}[!h]
	\begin{center}
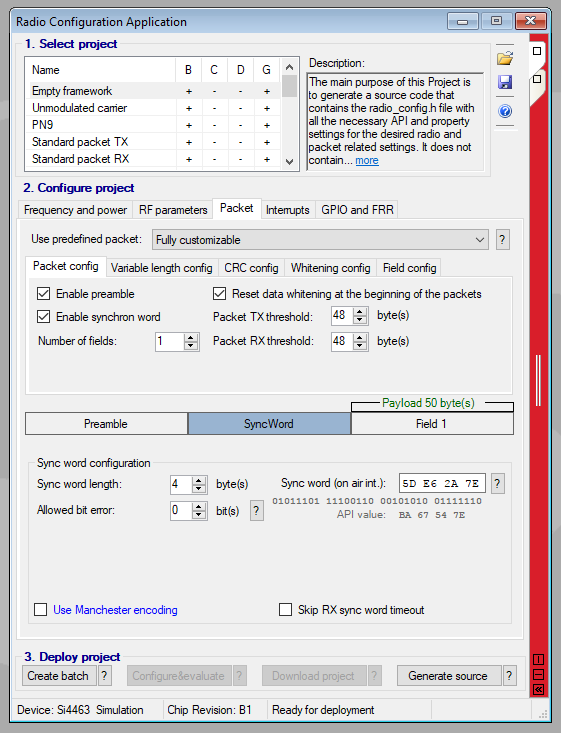
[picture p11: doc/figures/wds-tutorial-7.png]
		
		\caption{Step 7 of the radio configuration.}
		\label{fig:wds-tutorial-step-7}
	\end{center}
\end{figure}

\subsubsection{Step 8}

\begin{enumerate}
    \item In the ``Field 1" tab, change the ``Field length" to 50 bytes.
    \item Go to the next step.
\end{enumerate}

\begin{figure}[!h]
	\begin{center}
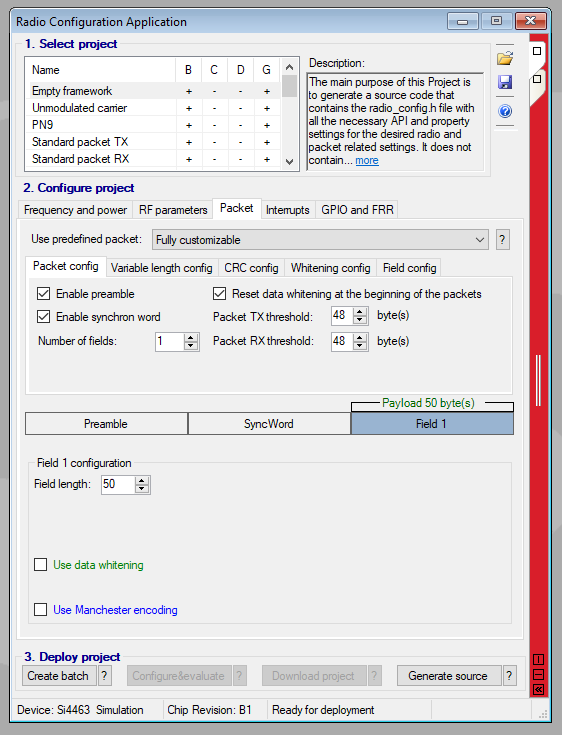
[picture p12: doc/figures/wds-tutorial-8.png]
		
		\caption{Step 8 of the radio configuration.}
		\label{fig:wds-tutorial-step-8}
	\end{center}
\end{figure}

\subsubsection{Step 9}

\begin{enumerate}
    \item In the ``Variable length config" tab, there is no values to change.
    \item Go to the next step.
\end{enumerate}

\begin{figure}[!h]
	\begin{center}
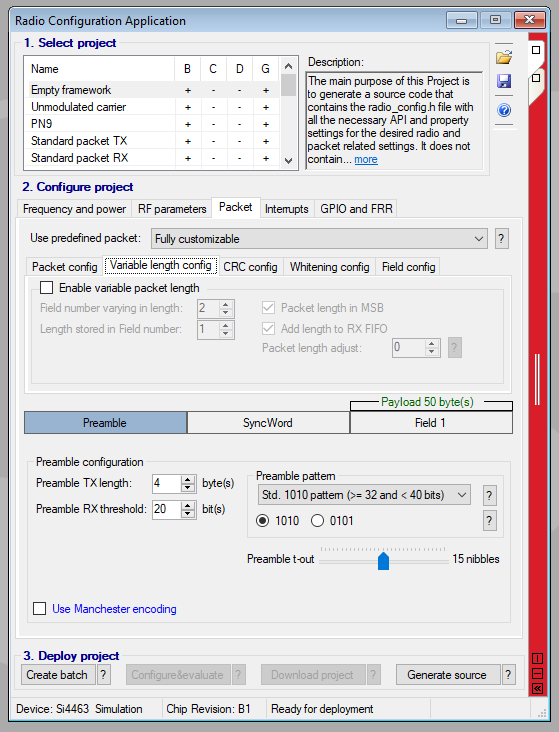
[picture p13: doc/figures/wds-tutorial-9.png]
		
		\caption{Step 9 of the radio configuration.}
		\label{fig:wds-tutorial-step-9}
	\end{center}
\end{figure}

\subsubsection{Step 10}

\begin{enumerate}
    \item In the ``CRC config" tab, choose ``No CRC." in ``CRC polynomial".
    \item Go to the next step.
\end{enumerate}

\begin{figure}[!h]
	\begin{center}
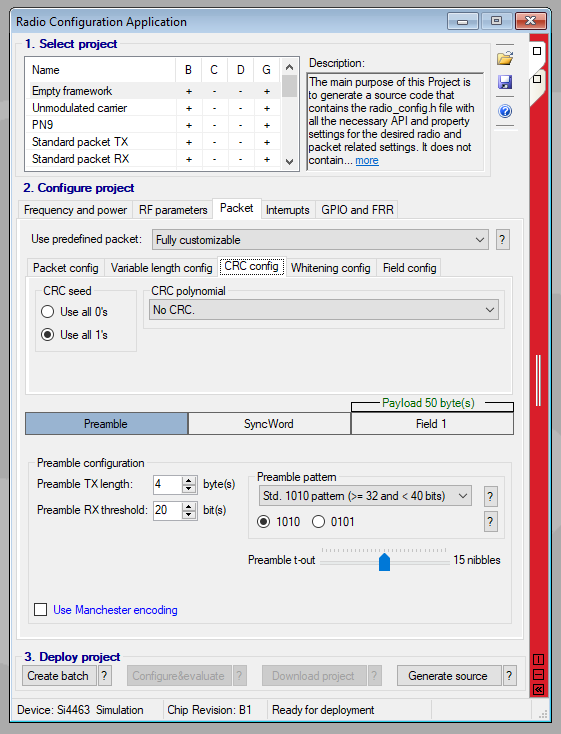
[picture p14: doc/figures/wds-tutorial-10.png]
		
		\caption{Step 10 of the radio configuration.}
		\label{fig:wds-tutorial-step-10}
	\end{center}
\end{figure}

\subsubsection{Step 11}

\begin{enumerate}
    \item In the ``Whitening config" tab, there is no values to change.
    \item Go to the next step.
\end{enumerate}

\begin{figure}[!h]
	\begin{center}
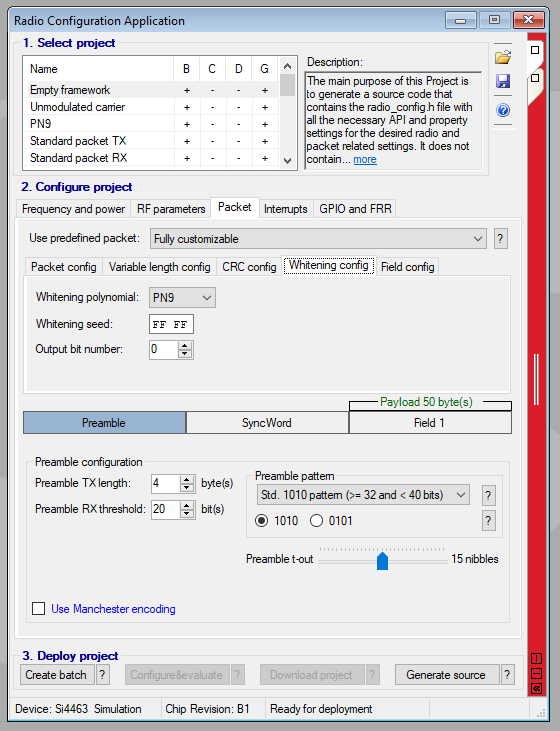
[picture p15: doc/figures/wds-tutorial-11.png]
		
		\caption{Step 11 of the radio configuration.}
		\label{fig:wds-tutorial-step-11}
	\end{center}
\end{figure}

\subsubsection{Step 12}

\begin{enumerate}
    \item In the ``Field config" tab, there is no values to change.
    \item Go to the next step.
\end{enumerate}

\begin{figure}[!h]
	\begin{center}
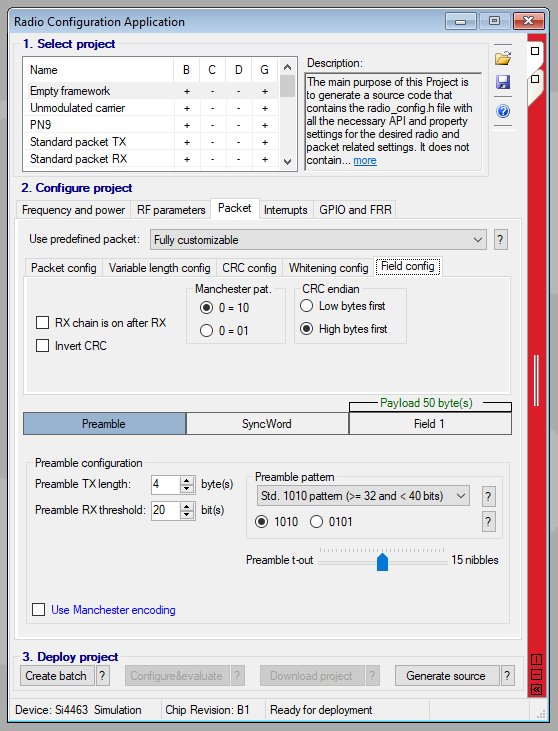
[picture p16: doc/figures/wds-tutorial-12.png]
		
		\caption{Step 12 of the radio configuration.}
		\label{fig:wds-tutorial-step-12}
	\end{center}
\end{figure}

\subsubsection{Step 13}

\begin{enumerate}
    \item In the ``Interrupts" tab, there is no values to change.
    \item Go to the next step.
\end{enumerate}

\begin{figure}[!h]
	\begin{center}
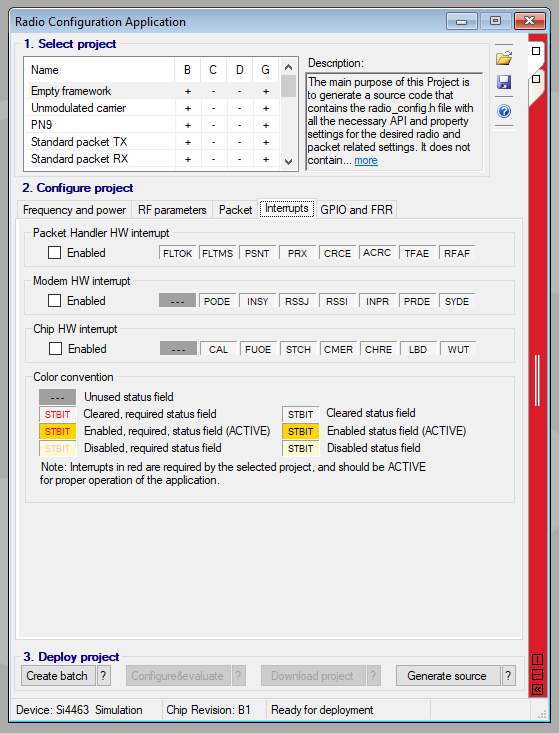
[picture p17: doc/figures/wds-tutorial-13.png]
		
		\caption{Step 13 of the radio configuration.}
		\label{fig:wds-tutorial-step-13}
	\end{center}
\end{figure}

\subsubsection{Step 14}

\begin{enumerate}
    \item In the ``GPIO and FRR" tab, enable pullup in GPIO1 and choose ``TX\_FIFO\_EMPTY - This output is..." as functionality.
    \item Enable pullup in GPIO2 and choose ``RX\_STATE - This output is..." as functionality.
    \item Enable pullup in GPIO3 and choose ``TX\_STATE - This output is..." as functionality.
    \item Enable pullup in NIRQ and choose ``Active low interrupt signal" as functionality.
    \item Enable pullup in SDO and choose ``SDO - Output SPI Serial data out." as functionality.
    \item Select ``Global status" for the ``Fast Response Register A".
    \item Select ``Global interrupt status" for the ``Fast Response Register B".
    \item Select ``Packet Handler status" for the ``Fast Response Register C".
    \item Select ``Chip status status" for the ``Fast Response Register D".
    \item Go to the next step.
\end{enumerate}

\begin{figure}[!h]
	\begin{center}
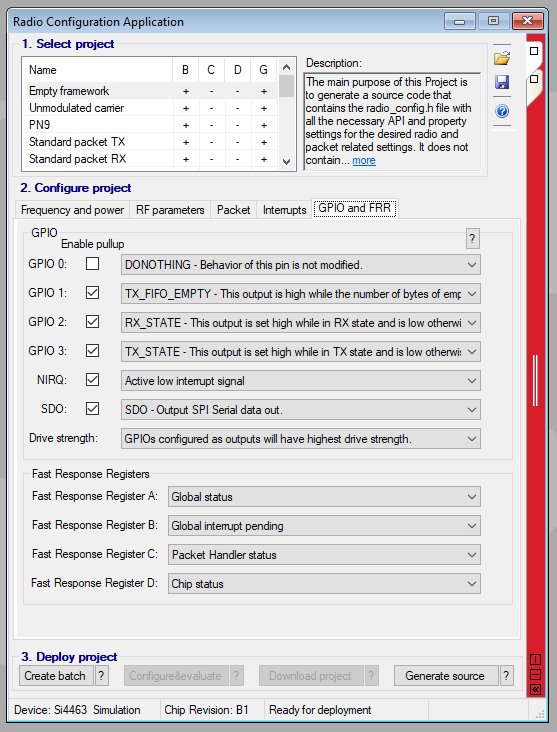
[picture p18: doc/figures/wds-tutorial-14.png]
		
		\caption{Step 14 of the radio configuration.}
		\label{fig:wds-tutorial-step-14}
	\end{center}
\end{figure}

\subsubsection{Step 15}

\begin{enumerate}
    \item Click in ``Generate Source" and select the ``.h" type of source.
    \item The software will ask where to save the generated file.
    \item The generated *.h file must be copied to the directory of the rf4463 driver.
\end{enumerate}

\subsection{Final Remarks}

This tutorial has the objective of generate a basic configuration parameters of the radio, some functionalities of the radio are not covered by the WDS software, and so, must be configured/controlled in the device driver.

\section{Compiling and Building the Beacon Firmware}

This tutorial is a reference to compile, build and flash the firmware of the beacon of the TTC module. All the software development was made using the Code Composer Studio (CCS) IDE, version 7.3.0. To load the code into the TTC MCU, the MSP-FET can be used.

\subsection{Creating the Project}

After the download and installation of the CCS, open it and create a new project with following steps:

\begin{enumerate}
    \item Go to ``File" -> ``New" -> ``CCS Project".
    \item The window from the figure \ref{fig:compiling-tutorial} will appear on the screen.
    \item On ``Target", select MSP430F6659.
    \item On ``Project name", enter the name of the project (It can be ``beacon", ``beacon\_firmware", or whatever name you want).
    \item On ``Project templates and examples" box, select ``Empty project".
    \item Click on ``Finish".
\end{enumerate}

\begin{figure}[!h]
	\begin{center}
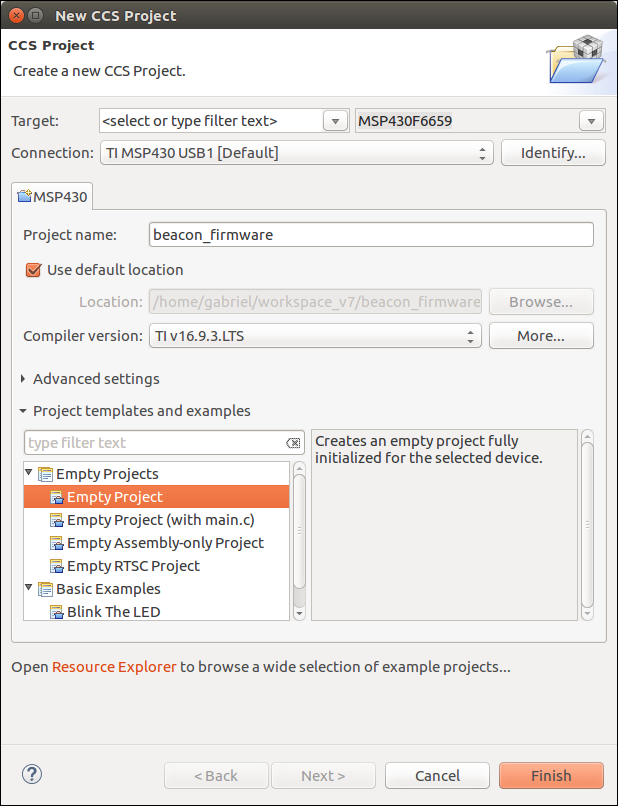
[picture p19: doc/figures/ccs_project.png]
		
		\caption{New CCS project window.}
		\label{fig:compiling-tutorial}
	\end{center}
\end{figure}

Now the beacon project with the correct parameters has been created, and the project source code files must be moved to the project directory. Copy the files inside the ``beacon" folder from the TTC git repository to the project folder.

\subsection{Compiling and Building}

To compile and build the firmware, click on "Project" -> "Build Project". If the process finish with no errors, the code is ready to go to the MCU of the beacon.

\subsection{Flashing}

To load the code into the board, connect the MSP-FET in the computer and follow the power-on tutorial.

With the board turned on and the MSP-FET connected, click on ``Run" -> ``Debug" or just press F11. If no errors occur, the firmware was loaded succesfully to the board.

\section{Power-On the TTC Module}

To power-on the TTC module, there are three different possibilities:

\begin{enumerate}
    \item Using three different power sources: one for the MCU, one for the beacon radio module and one for the telemetry radio module.
    \item Using two different power sources: one for each radio module (in this case, the beacon MCU is powered using the JTAG bus).
    \item Using just one power source to all components (THIS METHOD IS NOT SAFE: there is no control over the power consumption of each component).
\end{enumerate}

To test just the beacon, there is no need to power-on the telemetry radio module. Turning on the telemetry radio only makes sense if an external module is connected and controlling it (Like an OBC or an OBDH).

The connections reference of the TTC board can be found in External Connections.

\subsection{Using an External Power Source for the Beacon MCU}

\subsubsection{Power-On the Beacon MCU}

\begin{enumerate}
    \item Set an output of a channel of the power source to $3,3\ V$ and $30\ mA$ (Cut-off current).
    \item Connect the positive cable to the H2A-14 or H2B-14 pin of the PCI-104 connector.
    \item Connect the ground cable to any GND pin of the PCI-104 connector.
    \item Turn on this channel of the power source.
\end{enumerate}

\subsubsection{Power-On the Beacon Radio Module}

\begin{enumerate}
    \item Set another output of a channel of the power source to $5,0\ V$ and $500\ mA$ (Cut-off current).
    \item Connect the positive cable to the H1A-26 pin of the PCI-104 connector.
    \item Connect the ground cable to any GND pin of the PCI-104 connector.
    \item Turn on this channel of the power source.
\end{enumerate}

\subsubsection{Power-On the Telemetry Radio Module}

\begin{enumerate}
    \item Set another output of a channel of the power source to $5,0\ V$ and $500\ mA$ (Cut-off current).
    \item Connect the positive cable to the H1A-25 pin of the PCI-104 connector.
    \item Connect the ground cable to any GND pin of the PCI-104 connector.
    \item Turn on this channel of the power source.
\end{enumerate}

\subsection{Using the JTAG as Power Source for the Beacon MCU}

In this case, to power on the beacon MCU, just connect a jumper in the P4 connector of the board and after, connect a MSP-FET debbuger to the JTAG connector.

The procedure to power-on the radio modules is the same as above.

\section{Receiving the Beacon Data}

\subsection{Required Softwares}

\begin{itemize}
    \item GQRX (For just receive the signal).
    \item RTL-SDR drivers (The GRQX will install all the required drivers).
    \item FloripaSat GRS (For receive the signal and data).
\end{itemize}

\subsubsection{Supported SDRs}

\begin{itemize}
    \item RTL-SDR
    \item FunCube Dongle Pro+
\end{itemize}

\subsection{Receiving the Beacon Signal}

In this method, you will not be able to see the beacon data in real time. This only shows the presence of the beacon signals in the air.

The instructions to receive the beacon signal in the GQRX are available bellow:

\begin{enumerate}
    \item Open the GQRX software.
    \item Configure it for your SDR model.
    \item Press the power button on the upper left corner.
    \item Select the frequency to 145,9 MHz.
    \item Wait the spectrum of the beacon signal appear.
\end{enumerate}

The figure \ref{fig:beacon-signal-gqrx} illustrates the reception of the beacon signal in the GQRX software.

\begin{figure}[!h]
	\begin{center}
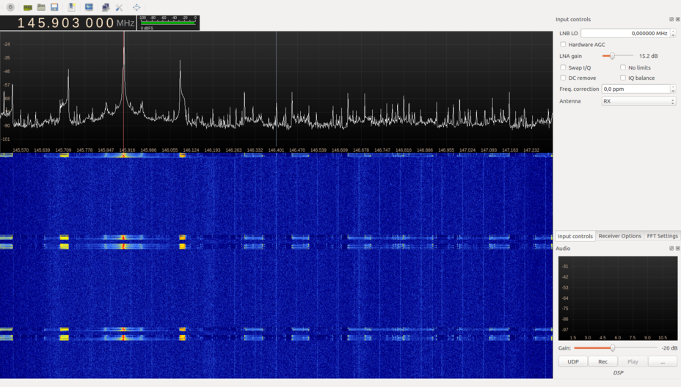
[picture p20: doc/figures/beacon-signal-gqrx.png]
		
		\caption{Beacon signal in GQRX.}
		\label{fig:beacon-signal-gqrx}
	\end{center}
\end{figure}

\subsection{Receiving the Beacon Data}

Using this method, you will be able to see the beacon (and the telemetry) data in real time on the computer screen. For that, the FloripaSat GRS sofware is required.

\begin{enumerate}
    \item Open the FloripaSat GRS software.
    \item Connect a the SDR device.
    \item Select the source of the signal.
    \item Press the play button in the beacon frame.
    \item A new window will appear in the screen, with the FFT and Waterfall plot of the received signal (in real time) of the connected SDR.
    \item Power on the beacon module of the TTC board.
    \item Adjust the frequency of the receive to the center frequency of the beacon signal (Use the FFT and the Waterfall plot for that).
    \item With the correct frequency sinthonization, the beacon data should appear in the main window of the FloripaSat GRS softwate.
\end{enumerate}

\begin{figure}[!h]
	\begin{center}
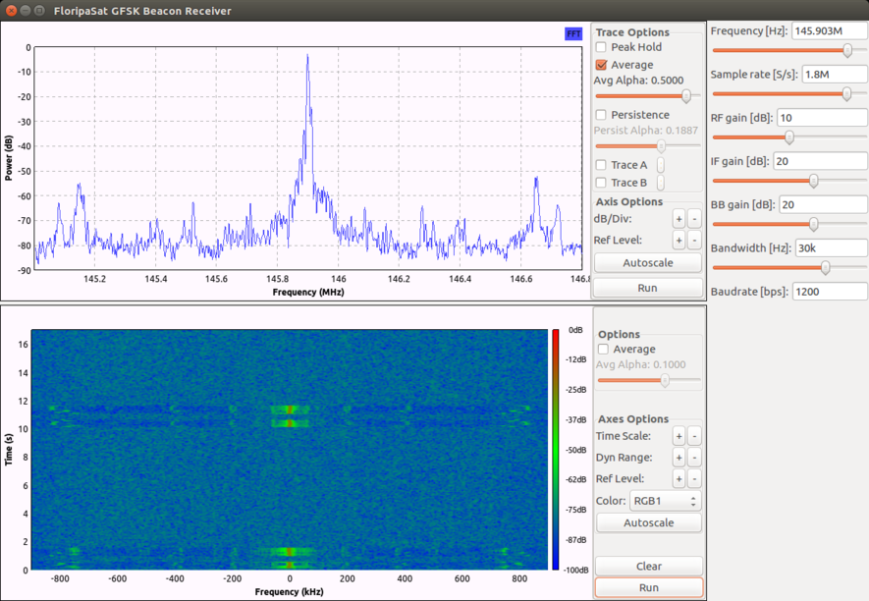
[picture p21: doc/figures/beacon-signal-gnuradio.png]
		
		\caption{Beacon signal in the GNURadio receiver from the FloripaSat GRS.}
		\label{fig:beacon-signal-gnuradio}
	\end{center}
\end{figure}

\begin{figure}[!h]
	\begin{center}
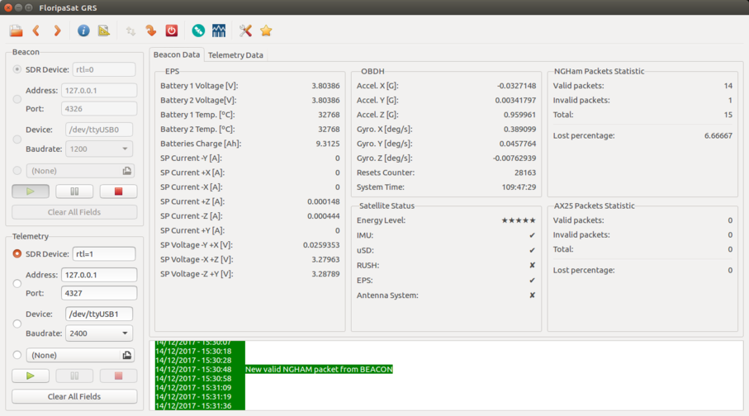
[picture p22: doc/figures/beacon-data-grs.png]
		
		\caption{Beacon data in the FloripaSat GRS.}
		\label{fig:beacon-data-grs}
	\end{center}
\end{figure}

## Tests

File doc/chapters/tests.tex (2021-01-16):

%
% tests.tex
%
% Copyright (C) 2021 by SpaceLab.
%
% TTC Documentation
%
% This work is licensed under the Creative Commons Attribution-ShareAlike 4.0
% International License. To view a copy of this license,
% visit http://creativecommons.org/licenses/by-sa/4.0/.
%

%
% \brief Tests chapter.
%
% \author Gabriel Mariano Marcelino <gabriel.mm8@gmail.com>
%
% \institution Universidade Federal de Santa Catarina (UFSC)
%
% \version 1.2.0
%
% \date 2021/01/16
%

\chapter{Tests} \label{ch:tests}

This...

\section{RF Signal Frequency}

\subsection{Beacon}

\begin{itemize}
    \item Target: 145,9 MHz
    \item Measurement: $\cong$ 145,9 MHz
\end{itemize}

\begin{figure}[H]
    \begin{center}
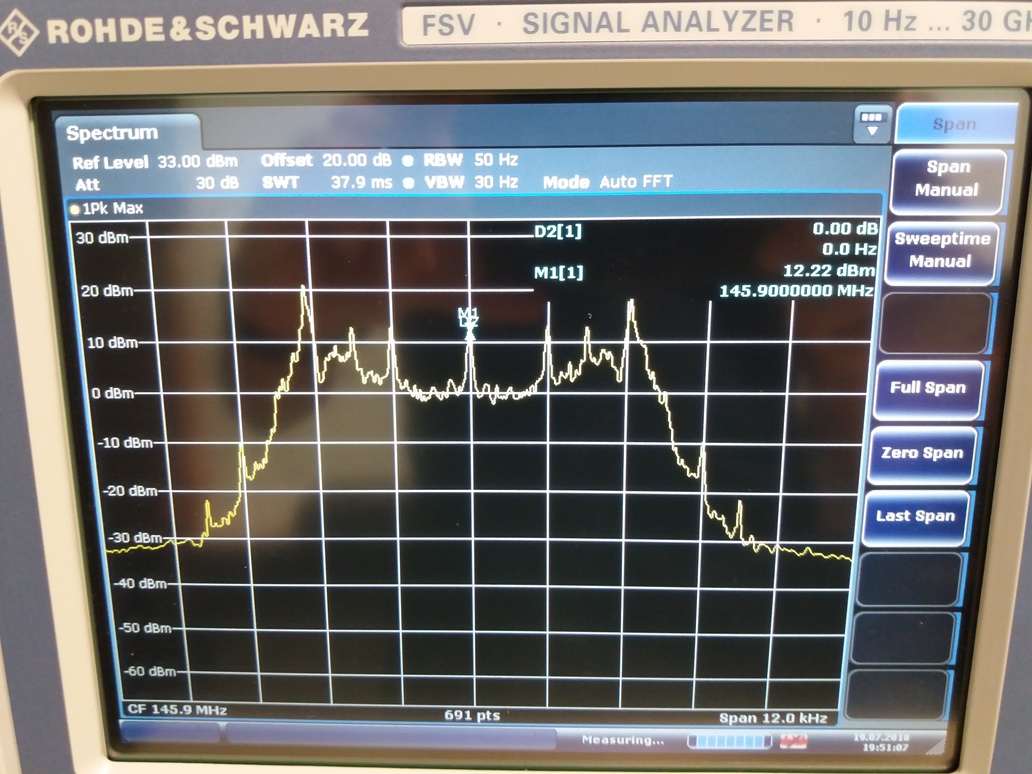
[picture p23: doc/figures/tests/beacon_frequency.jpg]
        
        \caption{Beacon output frequency.}
        \label{fig:beacon-frequency}
    \end{center}
\end{figure}

\subsection{Downlink}

\begin{itemize}
    \item Target: 437,9 MHz
    \item Measurement: $\cong$ 437,9 MHz
\end{itemize}

\begin{figure}[H]
    \begin{center}
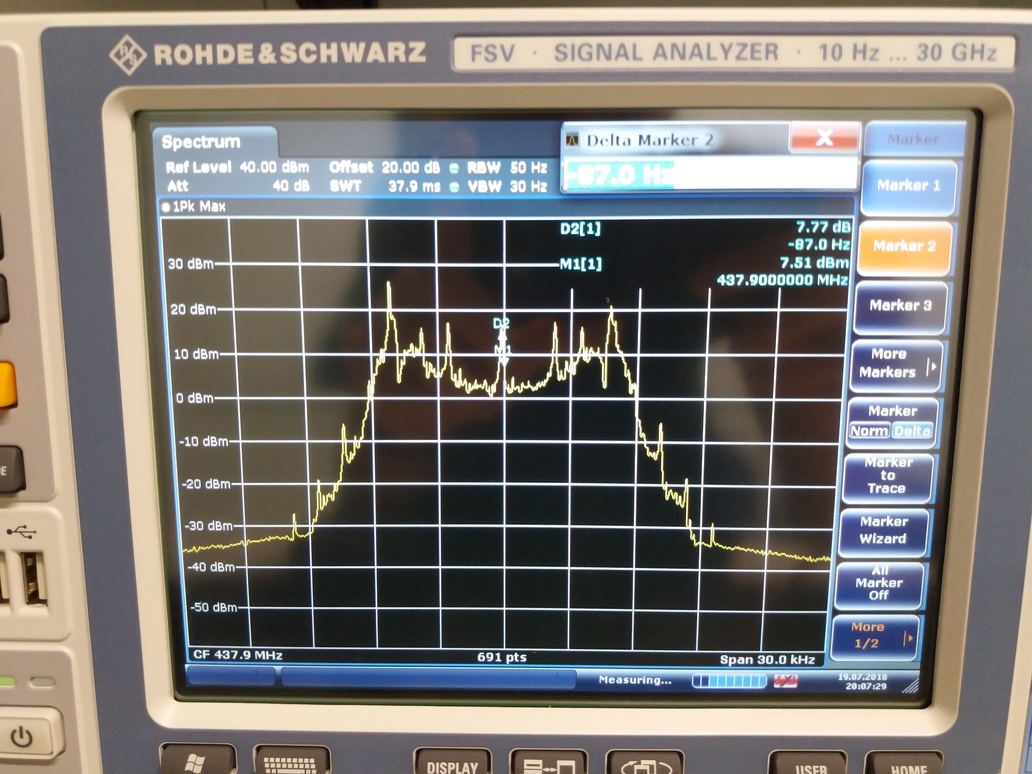
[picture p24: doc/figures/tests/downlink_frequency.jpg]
        
        \caption{Downlink output frequency.}
        \label{fig:downlink-frequency}
    \end{center}
\end{figure}

\section{RF Signal Power}

\subsection{Beacon}

\begin{itemize}
    \item Target: 30 dBm
    \item Measurement: $\cong$ 22 dBm (+3 dBm including the cable and connectors loss)
\end{itemize}

\begin{figure}[H]
    \begin{center}
        
        \caption{Beacon output power.}
        \label{fig:beacon-output-power}
    \end{center}
\end{figure}

\subsection{Downlink}

\begin{itemize}
    \item Target: 30 dBm
    \item Measurement: $\cong$ 27 dBm (+3 dBm including the cable and connectors loss)
\end{itemize}

The output power of the downlink radio can be seen in \autoref{fig:downlink-frequency}.

\section{Harmonics}

\subsection{Beacon}

\begin{figure}[H]
    \begin{center}
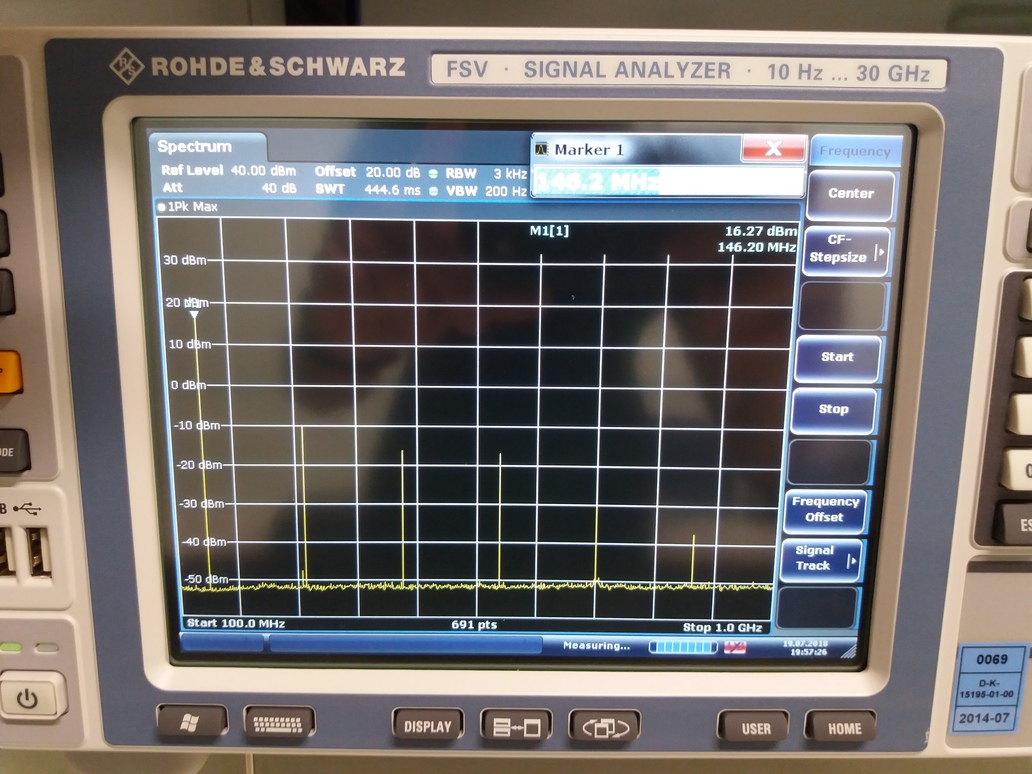
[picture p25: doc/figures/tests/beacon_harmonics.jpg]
        
        \caption{Beacon signal harmonics.}
        \label{fig:beacon-harmonics}
    \end{center}
\end{figure}

\begin{figure}[H]
    \begin{center}
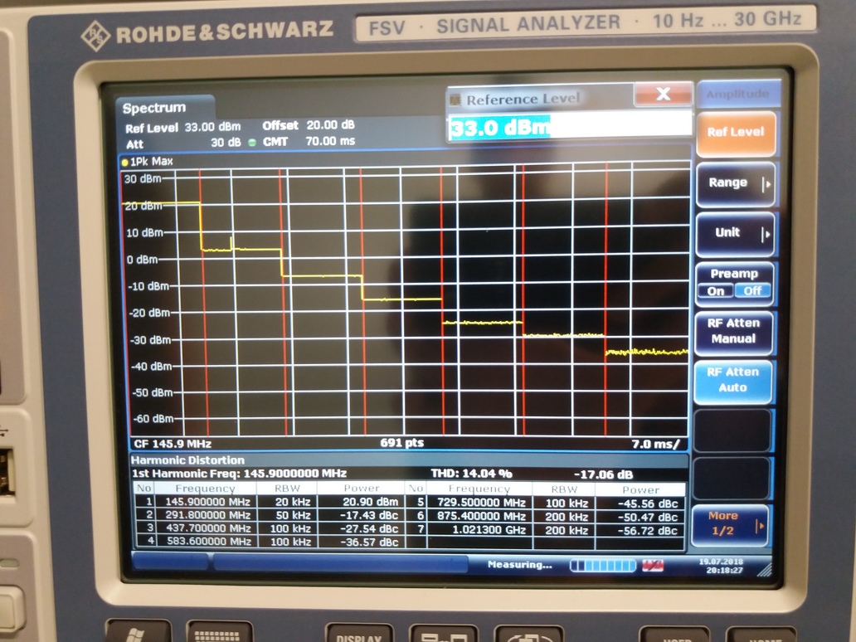
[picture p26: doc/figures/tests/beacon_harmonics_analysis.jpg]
        
        \caption{Analysis of the beacon signal harmonics.}
        \label{fig:beacon-harmonics-analysis}
    \end{center}
\end{figure}

\subsection{Downlink}

\begin{figure}[H]
    \begin{center}
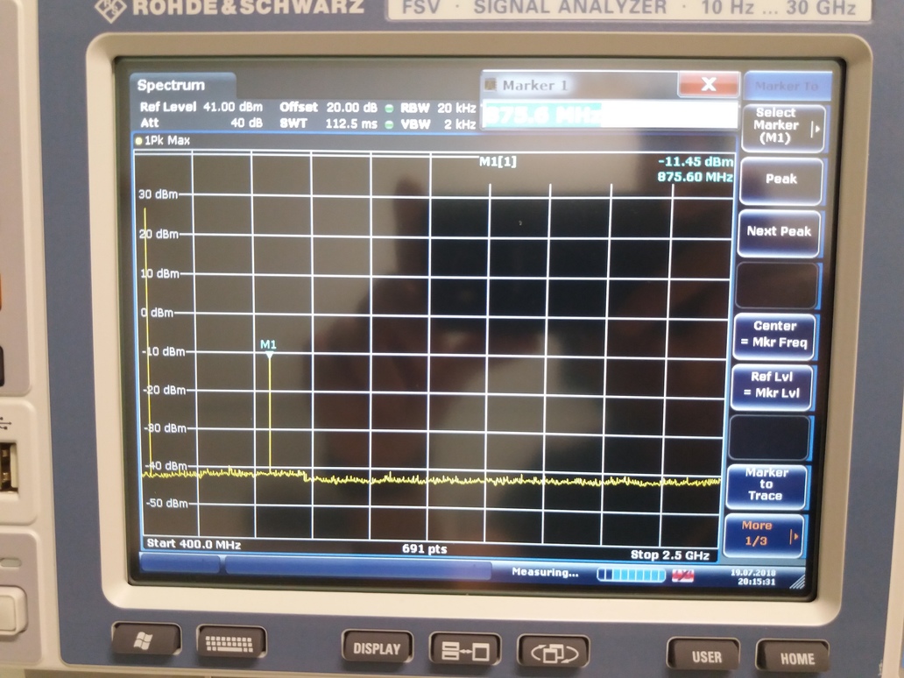
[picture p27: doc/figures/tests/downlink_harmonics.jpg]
        
        \caption{Downlink signal harmonics.}
        \label{fig:downlink-harmonics}
    \end{center}
\end{figure}

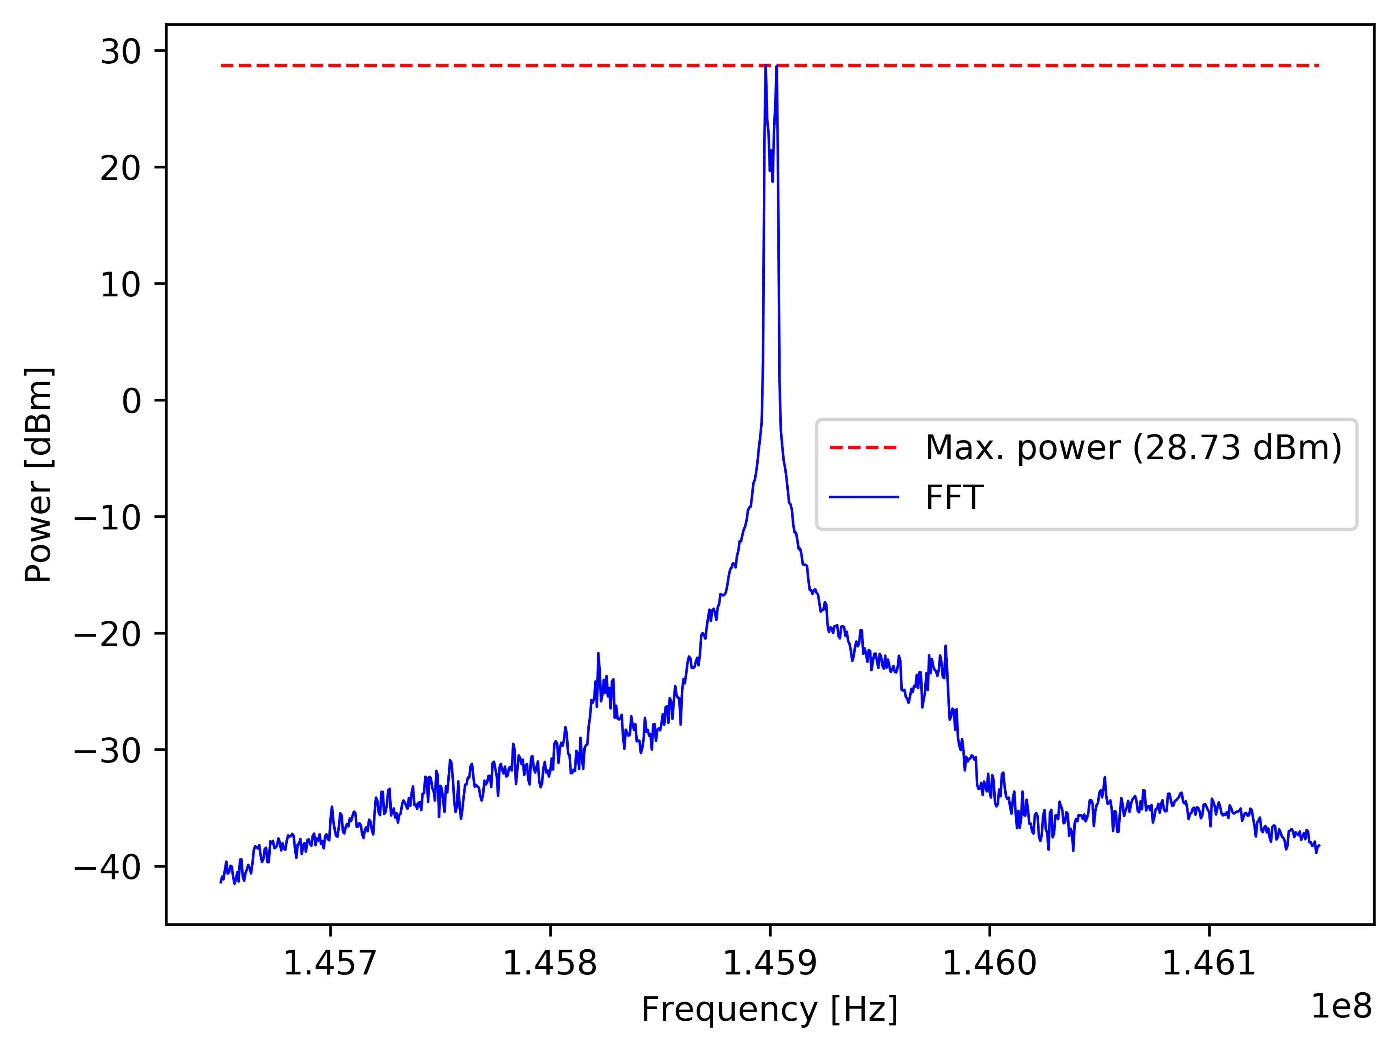
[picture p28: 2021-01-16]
doc/figures/tests/beacon_output_power.png

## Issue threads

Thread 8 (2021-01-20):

Firmware: Fix the NGHam library implementation

mgm8, 2021-01-20:
The FEC algorithm is not working properly in the current port of the NGHam library.

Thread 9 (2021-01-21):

Hardware: Update the standard of the Altium project according to the new standard

mgm8, 2021-01-21:
PCB standard: [https://github.com/spacelab-ufsc/pcb-standard](https://github.com/spacelab-ufsc/pcb-standard)

YanAzer, 2021-01-23:
@mgm8 this issue is the same as https://github.com/spacelab-ufsc/ttc/issues/1

mgm8, 2021-01-24:
@YanAzer maked as [duplicate](https://github.com/spacelab-ufsc/ttc/labels/duplicate)

Closed 2021-01-24.

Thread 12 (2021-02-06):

Hardware: verify TX UART to EPS communication

YanAzer, 2021-02-06:
Currently the EPS module sends telemetry data for the TTC MCU (beacon) through the H2-5 PC104 interface. For the PC104 EPS it is supossed to have a TX from the beacon on the H2-7 pin, but on the TTC PCB there is no connection associate with it.

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

YanAzer, 2021-03-02:
Linked issue #13

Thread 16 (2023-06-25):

Schematic and Board Documentation not synced

nilavghosh, 2023-06-25:
Hi Team,
Thanks for some brilliant work on building and sharing an open source cubesat.

I was studying your TTC and I think the documentation and the hardware schematic are not synced. Would be great if you can help confirm if this is so. I have looked at the v1.0 and v1.1 versions and see the same. Attaching screenshots below,

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

Regards,
Nilav

nilavghosh, 2023-07-05:
Hello @miguelboing @mgm8  . Just circling back to check :). If you can confirm the doc and the boards are out of sync that should be ok as well.

mgm8, 2023-07-07:
Hello @nilavghosh,

The documentation is outdated, the correct version of the PC104 pinout is the version presented in the schematics.

Thanks for findout the issue.

nilavghosh, 2023-07-07:
Thanks @mgm8 . Appreciate the response. Is there a newer version of the document? If not . I'll treat the schematic as the source of truth. Thanks .

Closed 2023-07-30.

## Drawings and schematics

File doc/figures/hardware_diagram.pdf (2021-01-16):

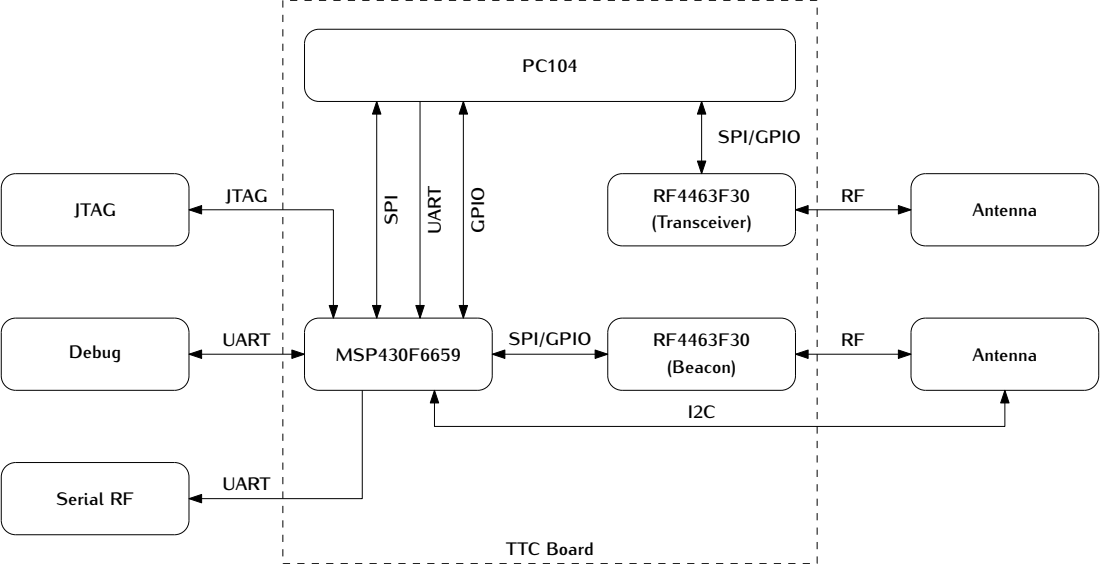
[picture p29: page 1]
MSP430F6659; RF4463F30 (Beacon) SPI/GPIO; RF4463F30 (Transceiver); Antenna RF; Antenna RF I2C JTAG Debug; SPI/GPIO SPI; UART; GPIO Serial RF; UART JTAG; TTC Board UART

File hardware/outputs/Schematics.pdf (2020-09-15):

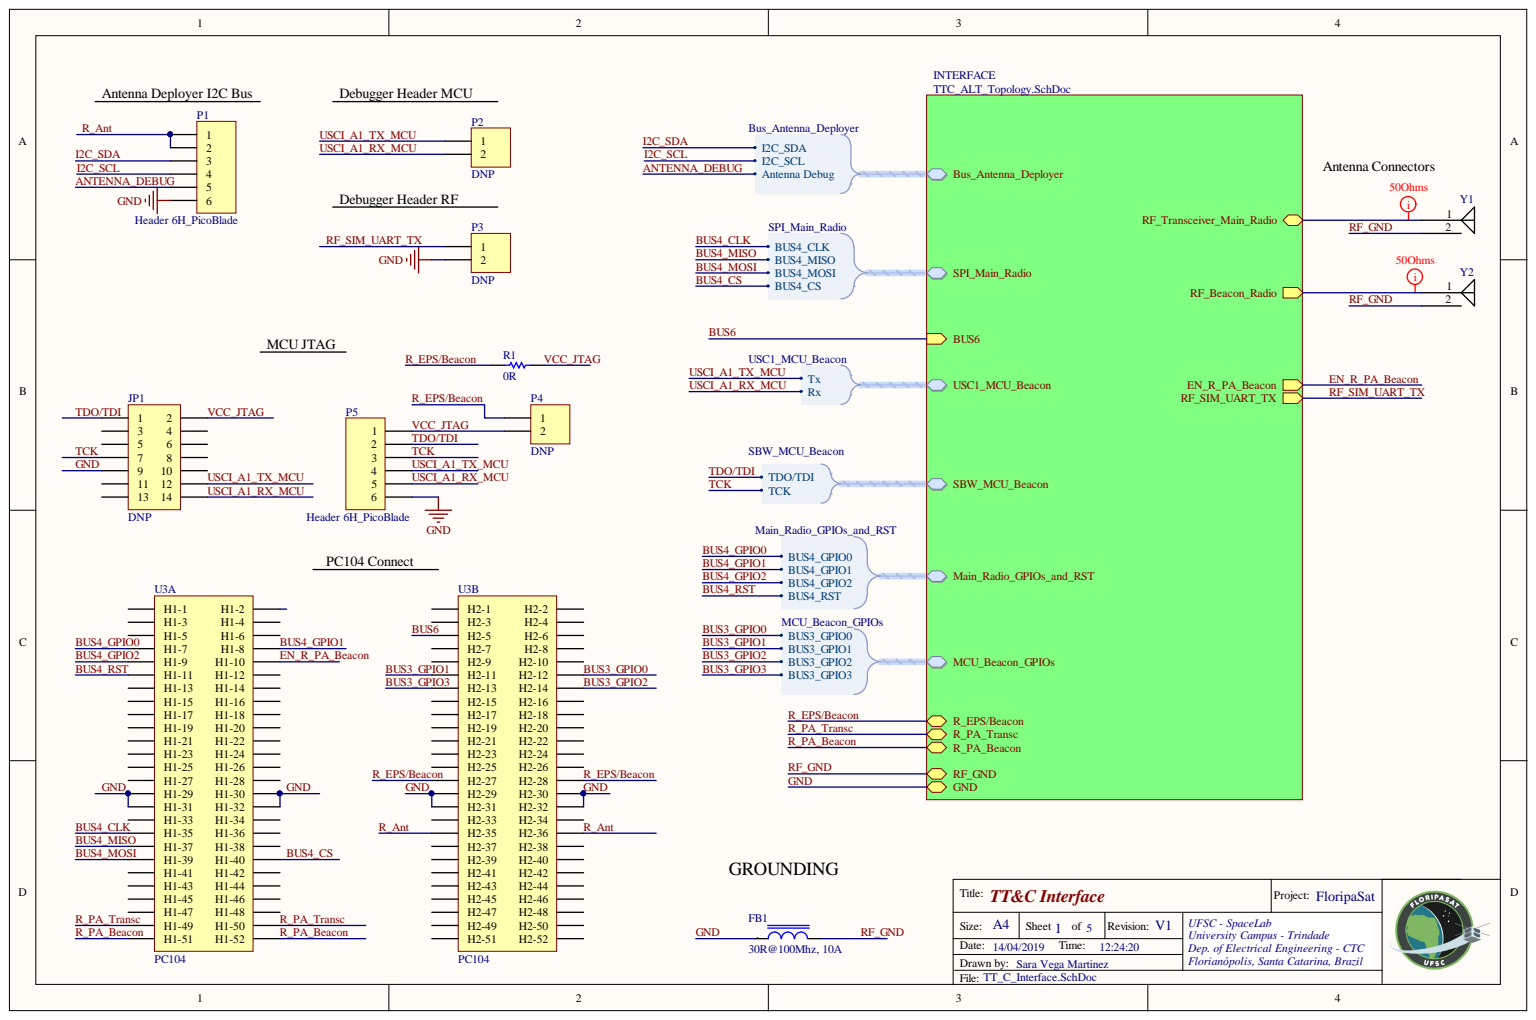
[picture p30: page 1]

Titl e : TT& C Inte rfac e | Proj e c t : FloripaSat

A4 S ize : | S h e e t 1 o f 5 | V1 R e vi s ion : | UFS C -Sp a c e La b Un i v e rsi ty Camp us -Tr i n dade Dep . of El e c t r i c a l Engine e r ing -C TC Fl o r i a n óp o l is, San ta Catari na, Bra z i l

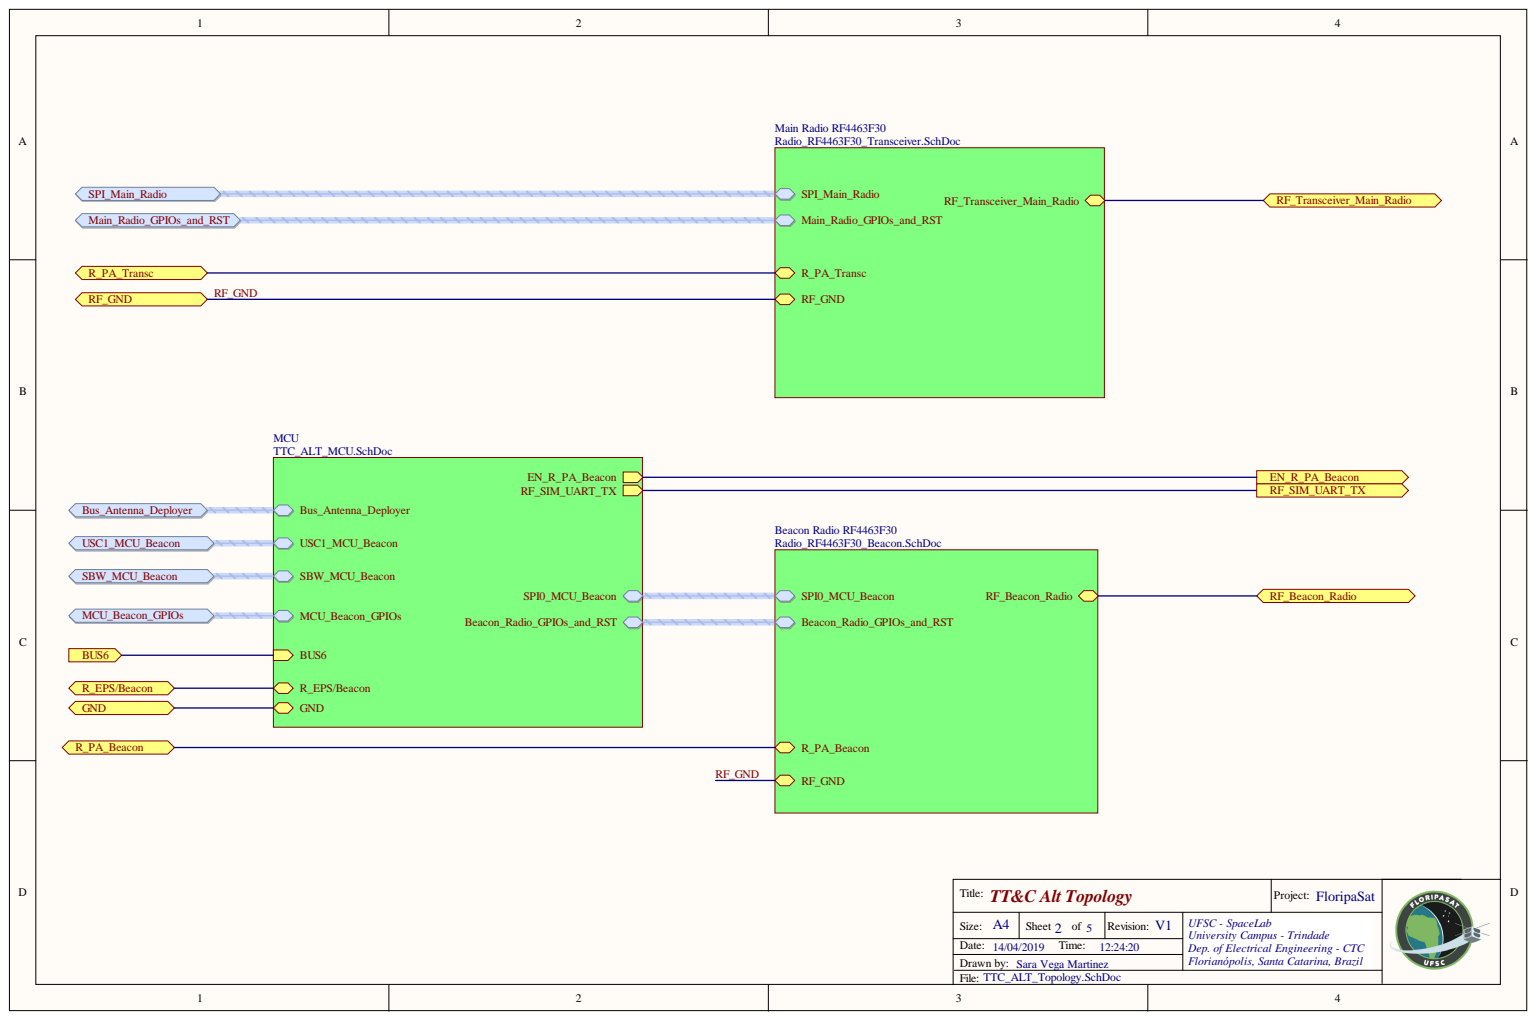
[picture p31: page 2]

Title: TT&C Alt Topology | Project: FloripaSat

A4 Size: | Sheet 2 of 5 | V1 Revision: | UFSC - SpaceLab University Campus - Trindade Dep. of Electrical Engineering - CTC Florianópolis, Santa Catarina, Brazil

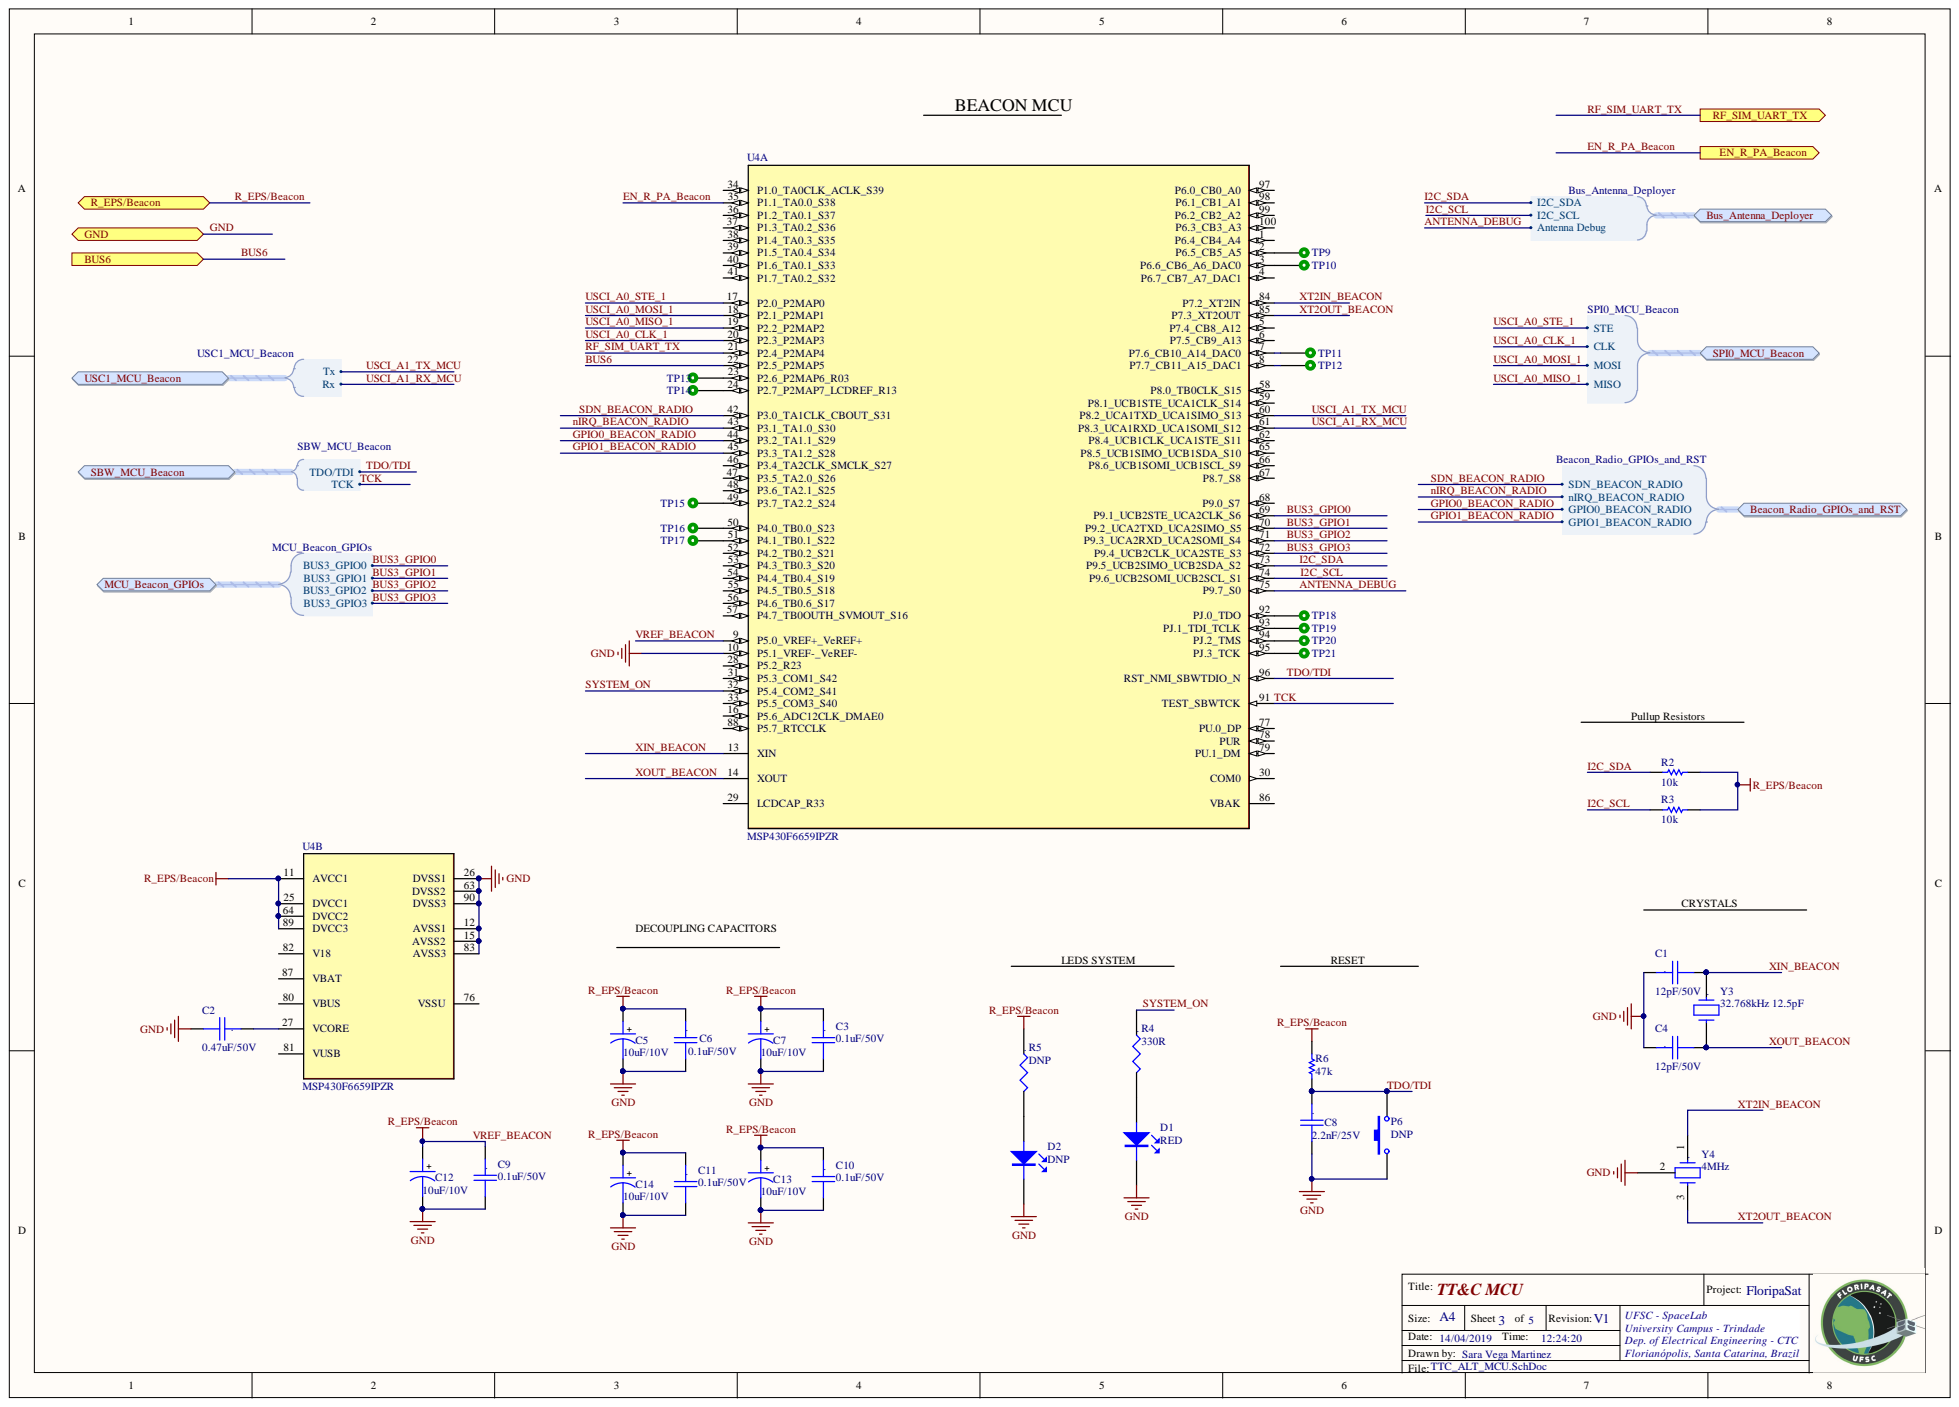
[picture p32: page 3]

Title: TT&C MCU | Project: FloripaSat

A4 Size: | Sheet of | V1 Revision: | UFSC - SpaceLab University Campus - Trindade Dep. of Electrical Engineering - CTC Florianópolis, Santa Catarina, Brazil

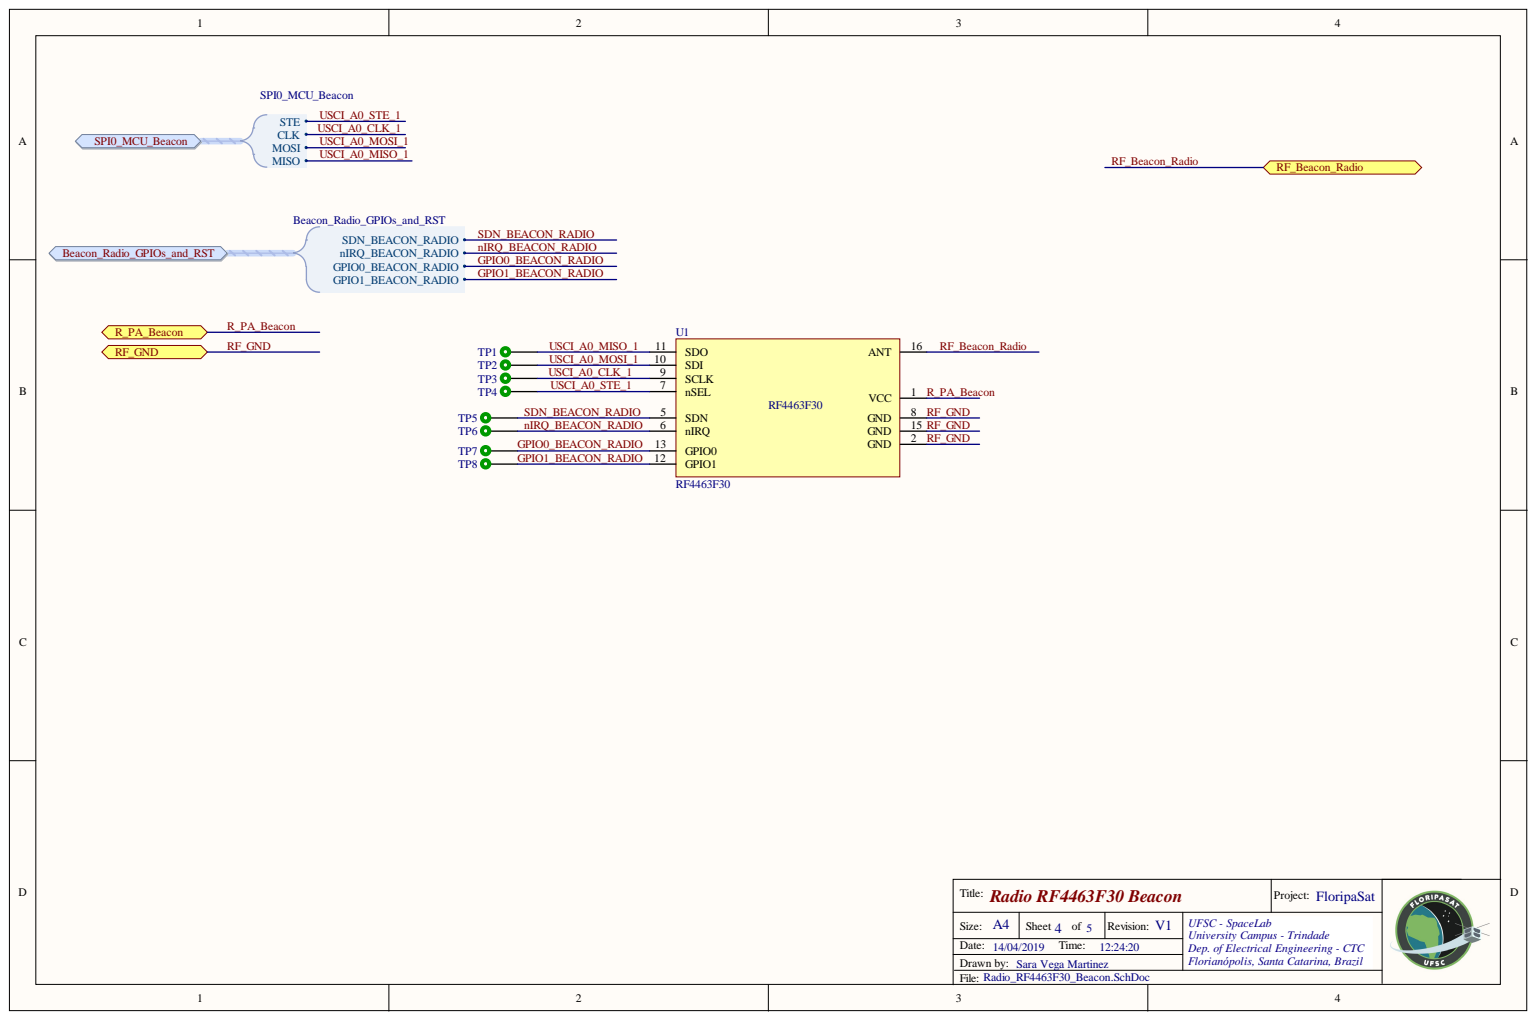
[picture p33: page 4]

Title: Radio RF4463F30 Beacon | Project: FloripaSat

A4 Size: | Sheet 4 of 5 | V1 Revision: | UFSC - SpaceLab University Campus - Trindade Dep. of Electrical Engineering - CTC Florianópolis, Santa Catarina, Brazil

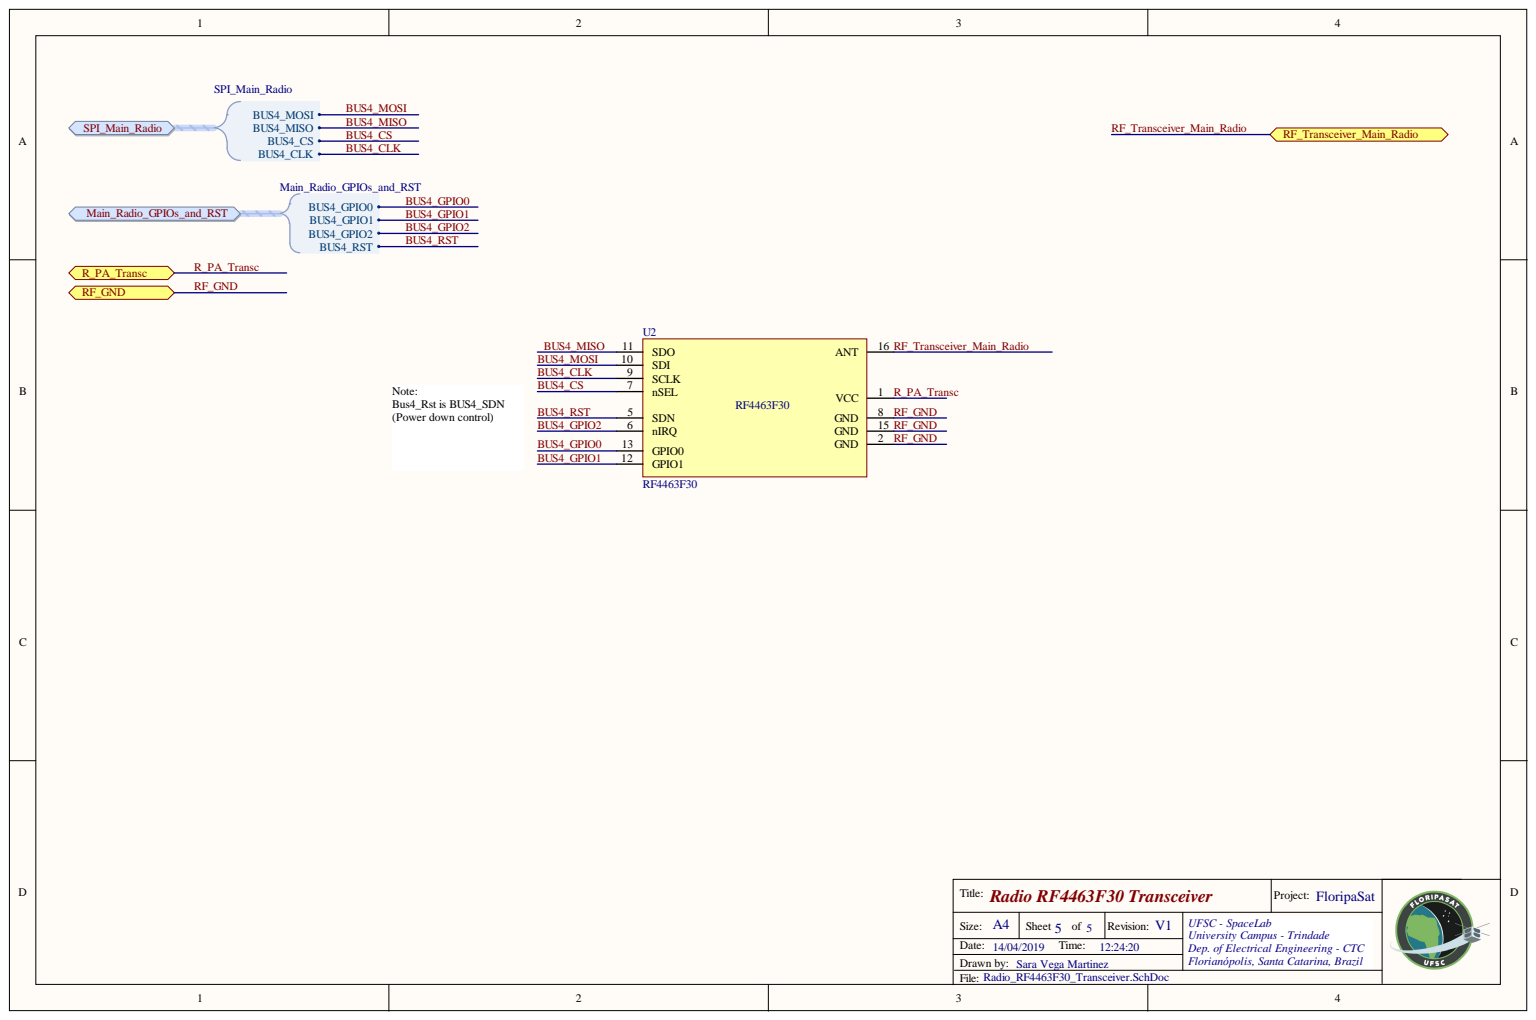
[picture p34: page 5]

Title: Radio RF4463F30 Transceiver | Project: FloripaSat

A4 Size: | Sheet 5 of 5 | V1 Revision: | UFSC - SpaceLab University Campus - Trindade Dep. of Electrical Engineering - CTC Florianópolis, Santa Catarina, Brazil

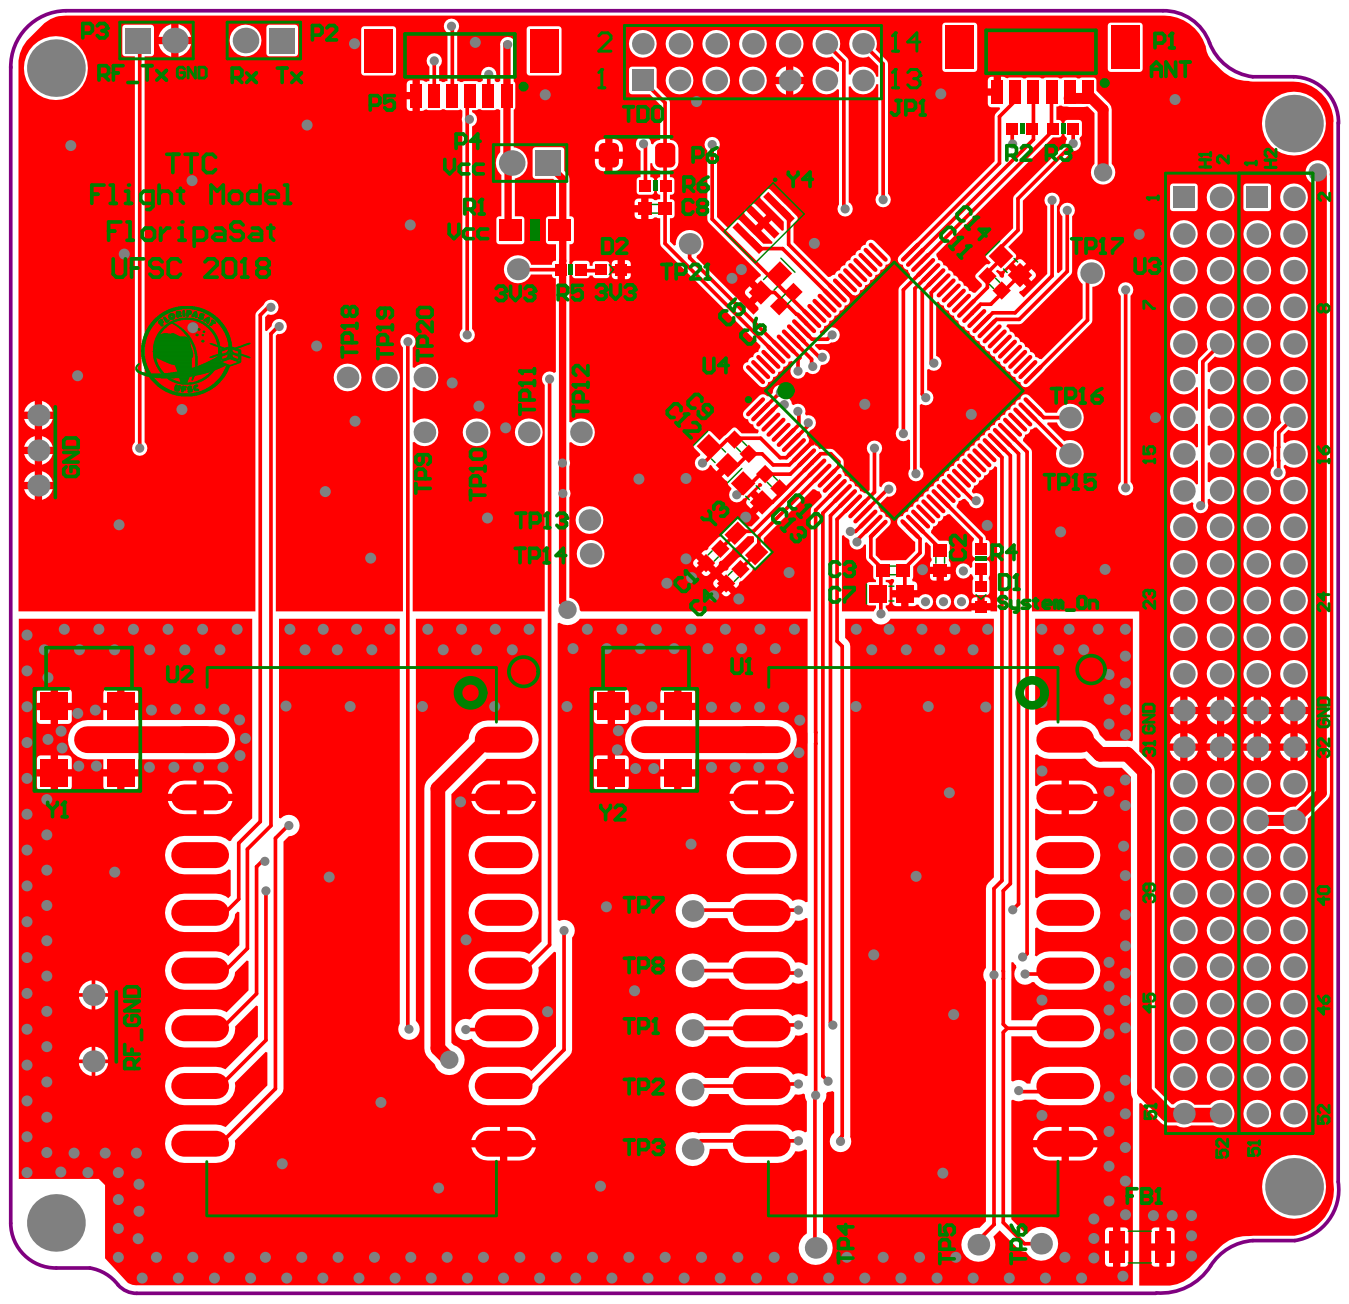
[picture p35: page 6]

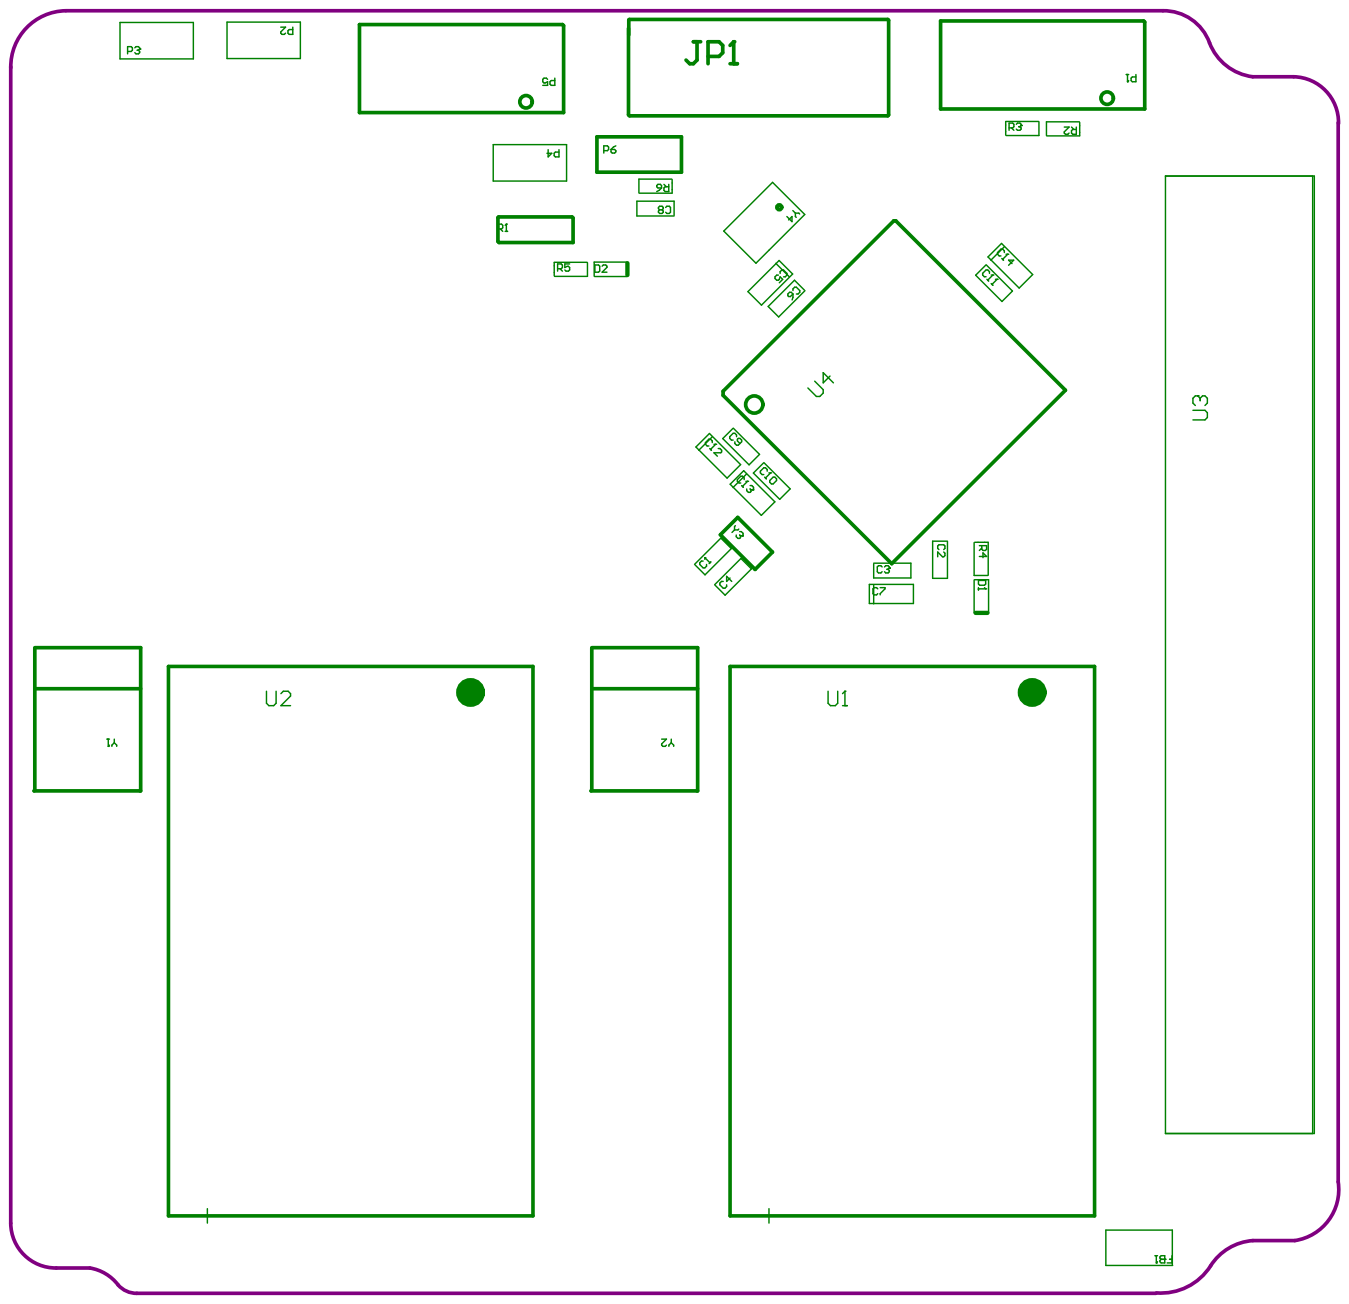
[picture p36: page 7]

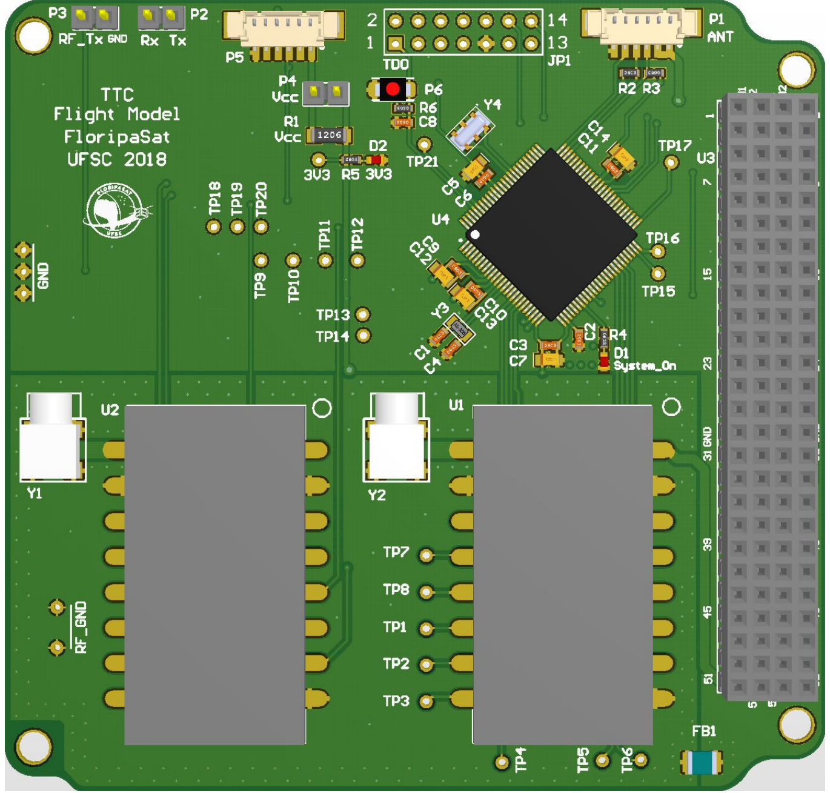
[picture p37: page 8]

Bill of Materials | TT&C Interface
Source Data From: | PCB_Project_TTC_Alt_RF4463F30.PrjPcb
Project: | | PCB_Project_TTC_Alt_RF4463F30.PrjPcb
Variant: | | None
Creation Date: 14/04/2019 | 12:24:39
Print Date: | 14-Apr-19 | 12:24:49 PM
Footprint | Comment | Partnumber | Designator | Description | Quantity
CC0603 | 12pF/50V | GQM1885C1H1
| | 20GB01D | C1, C4 | CAP CER 12pF 50V 0603 | 2
CC0603 | 0.47uF/50V | C1608X7R1H47
| | 4K080AE | C2 | CAP CER 0.47UF 50V 10% X7R 0603 | 1
CC0603 | 0.1uF/50V | GRM188R71H1
| | 04KA93D | C3, C6, C9, C10, C11 | CAP CER 0.1UF 50V 10% X7R 0603 | 5
CC0805_Tant alum | 10uF/10V | TPSR106K006R
| | 1000 | C5, C7, C12, C13, C14 | CAP Tantalum 10uF 6.3V 10% 0805 | 5
CC0603 | 2.2nF/25V | GCM188R71E4
| | 73KA37D | C8 | CAP CER 0.047UF 25V 0603 | 1
0603-LED | RED | LTST-
| | C191KFKT | D1 | SMD Red LED | 1
0603-LED | DNP | 150060VS75000 | D2 | SMD Green LED | 1
IND1210 | 30R@100Mhz,
| 10A | BLE32PN300SN
| | 1L | FB1 | Ferrite Bead 30 OHM 10A 100MHz | 1
HDR2X7 | DNP | 90131-0127 | JP1 | Header, 7-Pin, Dual row | 1
HDR6 PicoBlade | Header
| 6H_PicoBlade | 53398-0671 | P1, P5 | Header, 6-Pin, Right Angle | 2
HDR 1X2 | DNP | 826646-2 | P2, P3, P4 | Header, 2-Pin | 3
B3U-1000P | DNP | B3U-1000P | P6 | Tactile Switches Tactile Switch SPST-NO
| | | | Top Actuated Surface Mount | 1
1206 | 0R | CRCW12060000
| | Z0EAHP | R1 | RES 0.0 OHM 1/2W JUMP 1206 | 1
0603 | 10k | MCT0603MC100
| | 2FP500 | R2, R3 | RES 10K OHM 1/8W 1% 0603 | 2
0603 | 330R | CRCW0603330
| | RFKEAHP | R4 | RES 330R OHM 1/4W 1% 0603 | 1
0603 | DNP | MCT06030C100
| | 1FP500 | R5 | RES 1.0K OHM 1/8W 1% 0603 | 1
0603 | 47k | MCT0603MD470
| | 2DP500 | R6 | RES 47K OHM 1/8W 0.5% 0603 | 1
RF4463F30 | RF4463F30 | RF4463F30 | U1, U2 | RF4463F30 High Power Wireless
| | | | Transceiver Module | 2
PC104 | PC104 | TSW-126-07-G-
| | D | U3 | PC104 | 1
PZ0100A_N | MSP430F6659I
| PZR | MSP430F6659I
| | PZR | U4 | Imported | 1
CONN MCX JACK R/A 50 OHM SMD - duplicate | Coaxial_Connec
| tors_90º | 1-1337583-0 | Y1, Y2 | CONN MCX JACK R/A 50OHM SMD | 2
ABS06 0805 | 32.768kHz
12.5pF

ABS06-
32.768KHZ-T
Y3 | CRYSTAL 32.768KHZ 12.5PF SMD | 1

XTAL_CSTC
E_G15L
4MHz | CSTCR4M00G1
5L99-R0
Y4 | CER RESONATOR 4MHz SMD Murata | 1
| | 38
Approved | Notes

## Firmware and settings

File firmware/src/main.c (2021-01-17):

/*
 * main.c
 * 
 * Copyright (C) 2017-2019, Universidade Federal de Santa Catarina.
 * 
 * This file is part of FloripaSat-TTC.
 * 
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
 */

/**
 * \brief Main file.
 * 
 * \author Gabriel Mariano Marcelino <gabriel.mm8@gmail.com>
 * 
 * \version 0.5.7
 * 
 * \date 08/06/2017
 * 
 * \defgroup src Source
 * \{
 */

#include "beacon.h"

/**
 * \brief The main function.
 * 
 * After the initializations of the peripherals, the program stays
 * running in a infinite loop. If the program get out of the main
 * infinite loop (If any critical error occurs), there is a second
 * infinite loop to force an watchdog trigger.
 *
 * \image html beacon_main_flowchart.png "Beacon main flowchart" width=200px
 * 
 * \return None.
 */
void main()
{
    beacon_init();
    
    beacon_run();
    
    while(1);       // Safety infinite loop (If the code get out of the main loop, the watchdog will be triggered here)
}

//! \} End of src group

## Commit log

2020-09-15 Hardware: Adding project, outputs and fabrication files
    [BOM TTC.xlsx, PCB_Project_TTC_Alt_RF4463F30.PrjPcb, Pick Place for PCB_TTC.csv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]
2020-09-20 hardware: outputs: Fixing the BOM
    [BOM TTC.xlsx, ttc_bom.ods]

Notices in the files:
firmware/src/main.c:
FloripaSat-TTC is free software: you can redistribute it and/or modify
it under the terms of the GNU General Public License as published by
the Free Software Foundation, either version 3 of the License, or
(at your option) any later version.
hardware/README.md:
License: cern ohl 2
